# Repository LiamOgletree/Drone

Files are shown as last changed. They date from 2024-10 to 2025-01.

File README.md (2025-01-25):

Welcome! I'm designing a custom flight controller for drones. This Github page hosts all relevant files and technical details related to this effort, to include requisite project code and KiCAD schematic and PCB files.

The hardware design integrates STM32F446RE and ESP32-S3 microcontrollers, wireless and GPS (PA1616S) capabilities, and a custom IMU composed of an accelerometer and gyroscope (LSM6DSO32), barometer and temperature sensor (BMP388), and magnetometer (LIS2MDL). On the software side, I'm using STM32CubeIDE for my development environment; FreeRTOS for the OS; SPI for the LSM6DSO32, LIS2MDL, and BMP388 sensors; and DMA/UART for the PA1616S GPS receiver. Additionally, I use a Kalman Filter for state estimation &mdash; I would recommend <a href="https://github.com/rlabbe/Kalman-and-Bayesian-Filters-in-Python">this resource</a> for anyone interested in understanding Kalman Filters.

For the custom board design, I used <a href="https://www.kicad.org/">KiCAD</a> for schematic creation and the PCB layout and used <a href="https://jlcpcb.com/">JLCPCB</a> to manufacture physical boards. I'm sourcing drone components primarily from <a href="https://www.getfpv.com/">getfpv</a> (e.g., <a href="https://www.team-blacksheep.com/products/prod:sourceone_v5">this drone frame</a>) but there are many other FPV sites. Finally, for debugging purposes, I have a <a href="https://www.saleae.com/products/saleae-logic-pro-8">Saleae Logic Analyzer</a>.

See below for a functional overview of the code as it exists today:

Drone

Additionally, see below for layered 2D and rendered 3D images of the PCB design:

STM32-DRONE-FLIGHT-CONTROLLER-pcb

STM32-DRONE-FLIGHT-CONTROLLER-top

STM32-DRONE-FLIGHT-CONTROLLER-bottom

Please feel free to reach me at ogletreeliam@gmail.com with any questions or comments. Thank you!

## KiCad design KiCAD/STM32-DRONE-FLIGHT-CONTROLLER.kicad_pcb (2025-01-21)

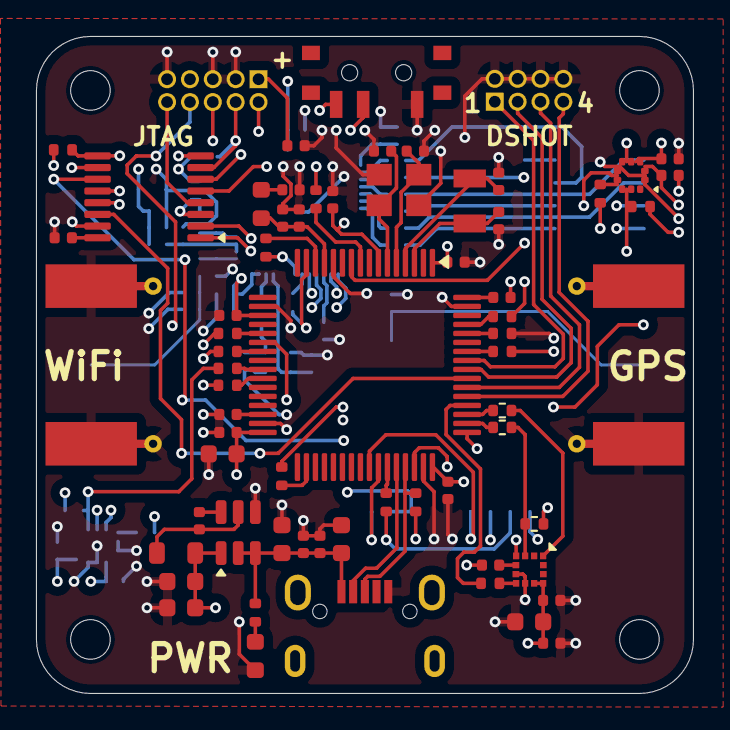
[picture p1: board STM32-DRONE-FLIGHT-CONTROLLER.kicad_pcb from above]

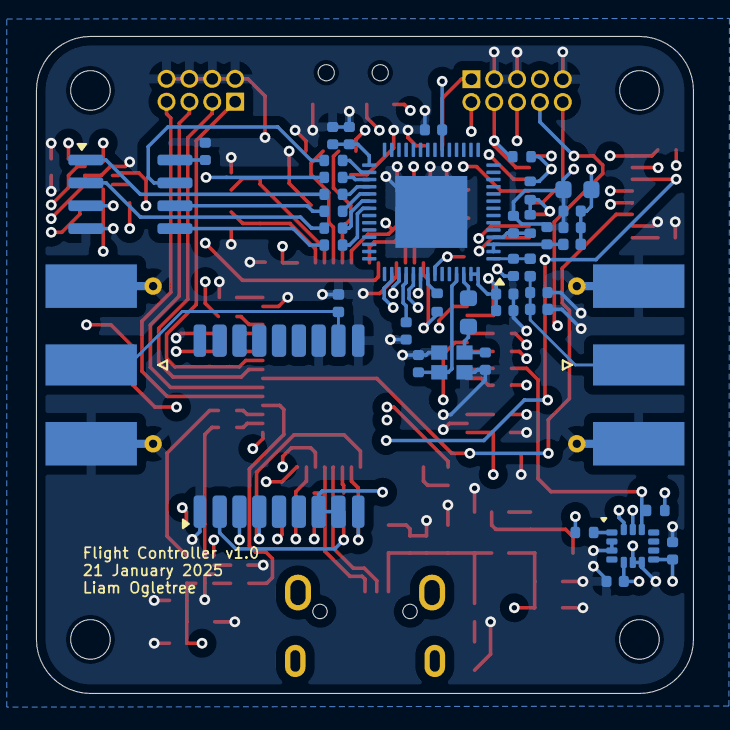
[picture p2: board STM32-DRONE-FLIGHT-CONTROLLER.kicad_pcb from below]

Board: 6 copper layers, 36.5 x 36.5 mm, 110 parts (42 on the bottom side), 88 nets.

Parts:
C1, C4, C8, C31, C44: 10uF; C_0603_1608Metric
C2, C21, C22, C23, C24, C35, C41, C45, C47, C48: 1uF; C_0402_1005Metric
C3, C5, C9, C10, C15, C16, C18, C19, C25, C26, C27, C28, C29, C30, C32, C37, C38, C39, C40, C42: 0.1uF; C_0402_1005Metric
C6, C7: 22uF; C_0603_1608Metric
C11, C12: 12.5pF; C_0402_1005Metric
C13, C14: 12pF; C_0402_1005Metric
C17: 2.2uF; C_0402_1005Metric
C20, C36: 10nF; C_0402_1005Metric
C33, C34: 10pF; C_0402_1005Metric
C43, C46: 1.2pF; C_0402_1005Metric
D1: Green; LED_0603_1608Metric
D2, D3: PESD0402-140; D_0402_1005Metric
FB1: 120R; L_0603_1608Metric
H1, H2, H3, H4: MountingHole; MountingHole_2.2mm_M2
J1: USB_B_Micro; USB_Micro-B_Wuerth_629105150521
J2: Conn_ARM_JTAG_SWD_10; PinHeader_2x05_P1.27mm_Vertical
J3: Conn_02x04_Odd_Even; PinHeader_2x04_P1.27mm_Vertical
J4, J5: Conn_Coaxial; SMA_Molex_73251-1153_EdgeMount_Horizontal
L1: 4.7uH; L_0805_2012Metric
L2: 24nH; L_0603_1608Metric
L3: 2nH; L_0402_1005Metric
L4: 2.4nH; L_0402_1005Metric
R1: 1k; R_0402_1005Metric
R2, R3, R4, R6, R7, R8, R9, R10, R18, R19, R20, R24, R25, R26, R27, R28, R29: 47R; R_0402_1005Metric
R5, R21, R22, R23, R31, R32: 10k; R_0402_1005Metric
R11, R12, R13, R14, R30: 33R; R_0402_1005Metric
R15: 1k5; R_0402_1005Metric
R16, R17: 100k; R_0402_1005Metric
SW1: SW_SPDT; SW_SPDT_PCM12
U1: AP63203WU; TSOT-23-6
U2: STM32F446RET6; LQFP-64_10x10mm_P0.5mm
U3: TMUX1574; TSSOP-16_4.4x5mm_P0.65mm
U4: ST_HLGA-10_2x2mm_P0.5mm_LayoutBorder3x2y
U5: LGA-12_2x2mm_P0.5mm
U6: LGA-14_3x2.5mm_P0.5mm_LayoutBorder3x4y
U7: MAX-M10S; ublox_MAX
U8: ESP32-S3; QFN-56-1EP_7x7mm_P0.4mm_EP4x4mm
U9: W25Q16JVSS; SOIC-8_3.9x4.9mm_P1.27mm
Y1: 32.768kHz; Crystal_SMD_3215-2Pin_3.2x1.5mm
Y2: 8MHz; Crystal_SMD_3225-4Pin_3.2x2.5mm
Y3: Crystal_GND24; Crystal_SMD_2016-4Pin_2.0x1.6mm

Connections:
+3.3V: C6.1, C7.1, C8.1, C9.1, C10.1, C15.1, C16.1, C19.1, C22.1, C23.1, C24.1, C26.2, C27.2, C28.2, C29.2, C30.2, C31.2, C32.2, C35.1, C36.1, C38.2, C39.2, C40.1, C41.1, C42.1, C44.1, C45.1, C48.1, FB1.1, J2.1 (VTref), L1.2, L3.2, R15.1, R16.1, R17.1, R21.1, R22.1, R23.1, R32.1, SW1.3 (C), U1.1 (FB), U2.1 (VBAT), U2.19 (VDD), U2.32 (VDD), U2.48 (VDD), U2.64 (VDD), U3.16 (VDD), U4.1 (VDDIO), U4.10 (VDD), U5.9 (VDD), U5.10 (VDDIO), U6.5 (VDDIO), U6.8 (VDD), U7.7 (VCC_IO), U7.8 (VCC), U8.20 (VDD3P3_RTC), U8.29 (VDD_SPI), U8.46 (VDD3P3_CPU), U8.55 (VDDA), U8.56 (VDDA), U9.8 (VCC)
+3.3VA: C20.1, C21.1, FB1.2, U2.13 (VDDA)
/Power/VBUS: C1.1, C2.1, C3.1, C4.1, J1.1 (VBUS), R1.1, U1.2 (EN), U1.3 (IN)
/STM32F446RET6/HSE_IN: C13.1, U2.5 (PH0), Y2.1
/STM32F446RET6/HSE_OUT: C14.1, U2.6 (PH1), Y2.3
/STM32F446RET6/LSE_IN: C11.1, U2.3 (PC14), Y1.1
/STM32F446RET6/LSE_OUT: C12.1, U2.4 (PC15), Y1.2
BMP388_CS: R14.1, R21.2, U4.6 (CS)
DSHOT1: J3.1, U2.57 (PB5)
DSHOT2: J3.3, U2.56 (PB4)
DSHOT3: J3.5, U2.54 (PD2)
DSHOT4: J3.7, U2.53 (PC12)
ESP32_MTCK: U3.6 (S2B), U8.44 (MTCK)
ESP32_MTDI: J2.8 (NC/TDI), U8.47 (MTDI)
ESP32_MTDO: U3.13 (S4B), U8.45 (MTDO)
ESP32_MTMS: U3.10 (S3B), U8.48 (MTMS)
ESP32_NRST: R31.1, R32.2, U3.3 (S1B)
GND: C1.2, C2.2, C3.2, C4.2, C6.2, C7.2, C8.2, C9.2, C10.2, C11.2, C12.2, C13.2, C14.2, C15.2, C16.2, C17.2, C18.2, C19.2, C20.2, C21.2, C22.2, C23.2, C24.2, C25.2, C26.1, C27.1, C28.1, C29.1, C30.1, C31.1, C32.1, C33.2, C34.2, C35.2, C36.2, C37.2, C38.1, C39.1, C40.2, C41.2, C42.2, C43.2, C44.2, C45.2, C46.2, C47.2, C48.2, D1.1 (K), D2.2 (A), D3.2 (A), J1.5 (GND), J2.3 (GND), J2.5 (GND), J2.9 (GNDDetect), J3.2, J3.4, J3.6, J3.8, J4.2 (Ext), J5.2 (Ext), R5.2, SW1.1 (A), U1.4 (GND), U2.12 (VSSA), U2.18 (VSS), U2.31 (VSS), U2.47 (VSS), U2.63 (VSS), U3.8 (GND), U3.15 (EN), U4.3 (GND), U4.8 (GND), U4.9 (GND), U5.6 (GND), U5.8 (GND), U6.2 (SDx), U6.3 (SCx), U6.6 (GND), U6.7 (GND), U7.1 (GND), U7.10 (GND), U7.12 (GND), U8.57 (GND), U9.4 (GND), Y2.2, Y2.4, Y3.2, Y3.4
LIS2MDL_CS: R8.2, R22.2, U5.3 (CS)
LSM6DSO32_CS: R3.1, R23.2, U6.12 (CS)
M10S_PPS: U2.41 (PA8), U7.4 (TIMEPULSE)
M10S_RESET: U2.42 (PA9), U7.9 (~RESET)
unnamed: C33.1, L2.1, Y3.1
unnamed: C37.1, L3.1, U8.2 (VDD3P3), U8.3 (VDD3P3)
unnamed: D1.2 (A), R1.2
unnamed: D2.1 (K), J4.1 (In), U7.11 (RF_IN)
unnamed: C46.1, D3.1 (K), J5.1 (In), L4.2
unnamed: SW1.2 (B), U3.1 (SEL)
unnamed: C5.1, U1.6 (BST)
unnamed: C5.2, L1.1, U1.5 (SW)
unnamed: R5.1, U2.60 (BOOT0)
unnamed: R11.2, U2.14 (PA0)
unnamed: R6.1, U2.21 (PA5)
unnamed: R7.1, U2.23 (PA7)
unnamed: R12.2, U2.43 (PA10)
unnamed: R8.1, U2.50 (PA15)
unnamed: R9.1, U2.26 (PB0)
unnamed: R13.2, U2.58 (PB6)
unnamed: R14.2, U2.61 (PB8)
unnamed: R10.1, U2.34 (PB13)
unnamed: R2.2, U2.9 (PC1)
unnamed: R3.2, U2.25 (PC5)
unnamed: R4.2, U2.51 (PC10)
unnamed: C17.1, U2.30 (VCAP_1)
unnamed: R18.2, U4.5 (SDO)
unnamed: C25.1, U5.5 (C1)
unnamed: R19.2, U5.7 (SDO)
unnamed: R20.2, U6.1 (SDO)
unnamed: C47.1, R31.2, U8.4 (CHIP_PU)
unnamed: C43.1, L4.1, U8.1 (LNA_IN)
unnamed: R27.2, U8.33 (SPICLK)
unnamed: R26.2, U8.32 (SPICS0)
unnamed: R29.2, U8.35 (SPID)
unnamed: R24.2, U8.30 (SPIHD)
unnamed: R28.2, U8.34 (SPIQ)
unnamed: R25.2, U8.31 (SPIWP)
unnamed: R30.2, U8.49 (U0TXD)
unnamed: C34.1, U8.53 (XTAL_N), Y3.3
unnamed: L2.2, U8.54 (XTAL_P)
SPI1_MISO: R20.1, U2.22 (PA6)
SPI1_MOSI: R7.2, U6.14 (SDI)
SPI1_SCK: R6.2, U6.13 (SCK)
SPI2_MISO: R18.1, U2.10 (PC2)
SPI2_MOSI: R2.1, U4.4 (SDI)
SPI2_SCK: R10.2, U4.2 (SCK)
SPI3_MISO: R19.1, U2.52 (PC11)
SPI3_MOSI: R9.2, U5.4 (SDI)
SPI3_SCK: R4.1, U5.1 (SCK)
SPICLK: R27.1, U9.6 (CLK)
SPICS0: R26.1, U9.1 (~CS)
SPID: R29.1, U9.5 (DI(IO0))
SPIHD: R24.1, U9.7 (IO3)
SPIQ: R28.1, U9.2 (DO(IO1))
SPIWP: R25.1, U9.3 (IO2)
STM32_NRST: C18.1, U2.7 (NRST), U3.2 (S1A)
STM32_SWCLK: U2.49 (PA14), U3.5 (S2A)
STM32_SWDIO: U2.46 (PA13), U3.11 (S3A)
STM32_SWO: U2.55 (PB3), U3.14 (S4A)
SWD_NRST: J2.10 (~RESET), U3.4 (D1)
SWD_SWCLK: J2.4 (SWCLK/TCK), R16.2, U3.7 (D2)
SWD_SWDIO: J2.2 (SWDIO/TMS), R17.2, U3.9 (D3)
SWD_SWO: J2.6 (SWO/TDO), U3.12 (D4)
UART4_MISO: R30.1, U2.15 (PA1)
UART4_MOSI: R11.1, U8.50 (U0RXD)
USART1_MISO: R12.1, U7.2 (TXD)
USART1_MOSI: R13.1, U7.3 (RXD)
USB_D+: J1.3 (D+), R15.2, U2.45 (PA12)
USB_D-: J1.2 (D-), U2.44 (PA11)

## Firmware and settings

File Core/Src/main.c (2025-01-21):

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
/* Includes ------------------------------------------------------------------*/
#include "main.h"
#include "cmsis_os.h"

/* USER CODE BEGIN Includes */
#include "taskBMP388.h"
#include "taskLIS2MDL.h"
#include "taskLSM6DSO32.h"
#include "taskPA1616S.h"
#include "taskStateMachine.h"
#include "taskShared.h"
/* USER CODE END Includes */

SPI_HandleTypeDef hspi1;

TIM_HandleTypeDef htim5;
TIM_HandleTypeDef htim11;

UART_HandleTypeDef huart1;
UART_HandleTypeDef huart2;
DMA_HandleTypeDef hdma_usart1_rx;

/* Definitions for defaultTask */
osThreadId_t defaultTaskHandle;
const osThreadAttr_t defaultTask_attributes = {
  .name = "defaultTask",
  .stack_size = 128 * 4,
  .priority = (osPriority_t) osPriorityLow,
};
/* Definitions for RunLogger */
osThreadId_t RunLoggerHandle;
const osThreadAttr_t RunLogger_attributes = {
  .name = "RunLogger",
  .stack_size = 1000 * 4,
  .priority = (osPriority_t) osPriorityBelowNormal7,
};
/* Definitions for RunBMP388 */
osThreadId_t RunBMP388Handle;
const osThreadAttr_t RunBMP388_attributes = {
  .name = "RunBMP388",
  .stack_size = 128 * 4,
  .priority = (osPriority_t) osPriorityNormal,
};
/* Definitions for RunLIS2MDL */
osThreadId_t RunLIS2MDLHandle;
const osThreadAttr_t RunLIS2MDL_attributes = {
  .name = "RunLIS2MDL",
  .stack_size = 128 * 4,
  .priority = (osPriority_t) osPriorityNormal,
};
/* Definitions for RunLSM6DSO32 */
osThreadId_t RunLSM6DSO32Handle;
const osThreadAttr_t RunLSM6DSO32_attributes = {
  .name = "RunLSM6DSO32",
  .stack_size = 128 * 4,
  .priority = (osPriority_t) osPriorityNormal,
};
/* Definitions for RunStateMachine */
osThreadId_t RunStateMachineHandle;
const osThreadAttr_t RunStateMachine_attributes = {
  .name = "RunStateMachine",
  .stack_size = 8192 * 4,
  .priority = (osPriority_t) osPriorityNormal,
};
/* Definitions for runPA1616S */
osThreadId_t runPA1616SHandle;
const osThreadAttr_t runPA1616S_attributes = {
  .name = "runPA1616S",
  .stack_size = 6000 * 4,
  .priority = (osPriority_t) osPriorityNormal,
};
/* Definitions for loggerMutex */
osMutexId_t loggerMutexHandle;
const osMutexAttr_t loggerMutex_attributes = {
  .name = "loggerMutex"
};
/* Definitions for smMutex */
osMutexId_t smMutexHandle;
const osMutexAttr_t smMutex_attributes = {
  .name = "smMutex"
};
/* Definitions for pa1616sMutex */
osMutexId_t pa1616sMutexHandle;
const osMutexAttr_t pa1616sMutex_attributes = {
  .name = "pa1616sMutex"
};
/* Definitions for loggerSemaphore */
osSemaphoreId_t loggerSemaphoreHandle;
const osSemaphoreAttr_t loggerSemaphore_attributes = {
  .name = "loggerSemaphore"
};
/* Definitions for smSemaphore */
osSemaphoreId_t smSemaphoreHandle;
const osSemaphoreAttr_t smSemaphore_attributes = {
  .name = "smSemaphore"
};
/* Definitions for pa1616sSemaphore */
osSemaphoreId_t pa1616sSemaphoreHandle;
const osSemaphoreAttr_t pa1616sSemaphore_attributes = {
  .name = "pa1616sSemaphore"
};
/* USER CODE BEGIN PV */
RingBuffer logger_ringbuffer;
RingBuffer sm_ringbuffer;
RingBuffer pa1616s_ringbuffer;
RingBuffer_t logger_ringbuffer_buf[64];
RingBuffer_t sm_ringbuffer_buf[64];
RingBuffer_t pa1616s_ringbuffer_buf[64];

TASK_ARGS task_args = {.hspi = &hspi1,
                       .huart_logger = &huart2,
                       .huart_pa1616s = &huart1,
                       .logger_ringbuffer = &logger_ringbuffer,
                       .sm_ringbuffer = &sm_ringbuffer,
                       .pa1616s_ringbuffer = &pa1616s_ringbuffer,
                       .logger_semaphore = &loggerSemaphoreHandle,
                       .sm_semaphore = &smSemaphoreHandle,
                       .pa1616s_semaphore = &pa1616sSemaphoreHandle,
                       .logger_mutex = &loggerMutexHandle,
                       .sm_mutex = &smMutexHandle};
/* USER CODE END PV */

void SystemClock_Config(void);
static void MX_GPIO_Init(void);
static void MX_DMA_Init(void);
static void MX_USART2_UART_Init(void);
static void MX_SPI1_Init(void);
static void MX_TIM5_Init(void);
static void MX_TIM11_Init(void);
static void MX_USART1_UART_Init(void);
void StartDefaultTask(void *argument);
extern void StartLogger(void *argument);
extern void StartBMP388(void *argument);
extern void StartLIS2MDL(void *argument);
extern void StartLSM6DSO32(void *argument);
extern void StartStateMachine(void *argument);
extern void StartPA1616S(void *argument);

/**
  * @brief  The application entry point.
  * @retval int
  */
int main(void)
{

  /* MCU Configuration--------------------------------------------------------*/

  /* Reset of all peripherals, Initializes the Flash interface and the Systick. */
  HAL_Init();

  /* Configure the system clock */
  SystemClock_Config();

  /* Initialize all configured peripherals */
  MX_GPIO_Init();
  MX_DMA_Init();
  MX_USART2_UART_Init();
  MX_SPI1_Init();
  MX_TIM5_Init();
  MX_TIM11_Init();
  MX_USART1_UART_Init();
  /* USER CODE BEGIN 2 */

  RingBuffer_ctor(&logger_ringbuffer, 64, logger_ringbuffer_buf);
  RingBuffer_ctor(&sm_ringbuffer, 64, sm_ringbuffer_buf);
  RingBuffer_ctor(&pa1616s_ringbuffer, 64, pa1616s_ringbuffer_buf);
  HAL_Delay(100);

  RCC->APB1ENR |= RCC_APB1ENR_TIM2EN;
  TIM5->CR1 |= TIM_CR1_CEN;

  /* USER CODE END 2 */

  /* Init scheduler */
  osKernelInitialize();
  /* Create the mutex(es) */
  /* creation of loggerMutex */
  loggerMutexHandle = osMutexNew(&loggerMutex_attributes);

  /* creation of smMutex */
  smMutexHandle = osMutexNew(&smMutex_attributes);

  /* creation of pa1616sMutex */
  pa1616sMutexHandle = osMutexNew(&pa1616sMutex_attributes);

  /* USER CODE BEGIN RTOS_MUTEX */
  /* add mutexes, ... */
  /* USER CODE END RTOS_MUTEX */

  /* Create the semaphores(s) */
  /* creation of loggerSemaphore */
  loggerSemaphoreHandle = osSemaphoreNew(64, 0, &loggerSemaphore_attributes);

  /* creation of smSemaphore */
  smSemaphoreHandle = osSemaphoreNew(64, 0, &smSemaphore_attributes);

  /* creation of pa1616sSemaphore */
  pa1616sSemaphoreHandle = osSemaphoreNew(64, 0, &pa1616sSemaphore_attributes);

  /* USER CODE BEGIN RTOS_SEMAPHORES */
  /* add semaphores, ... */
  /* USER CODE END RTOS_SEMAPHORES */

  /* USER CODE BEGIN RTOS_TIMERS */
  /* start timers, add new ones, ... */
  /* USER CODE END RTOS_TIMERS */

  /* USER CODE BEGIN RTOS_QUEUES */
  /* add queues, ... */
  /* USER CODE END RTOS_QUEUES */

  /* Create the thread(s) */
  /* creation of defaultTask */
  defaultTaskHandle = osThreadNew(StartDefaultTask, NULL, &defaultTask_attributes);

  /* creation of RunLogger */
  RunLoggerHandle = osThreadNew(StartLogger, (void*) &task_args, &RunLogger_attributes);

  /* creation of RunBMP388 */
  RunBMP388Handle = osThreadNew(StartBMP388, (void*) &task_args, &RunBMP388_attributes);

  /* creation of RunLIS2MDL */
  RunLIS2MDLHandle = osThreadNew(StartLIS2MDL, (void*) &task_args, &RunLIS2MDL_attributes);

  /* creation of RunLSM6DSO32 */
  RunLSM6DSO32Handle = osThreadNew(StartLSM6DSO32, (void*) &task_args, &RunLSM6DSO32_attributes);

  /* creation of RunStateMachine */
  RunStateMachineHandle = osThreadNew(StartStateMachine, (void*) &task_args, &RunStateMachine_attributes);

  /* creation of runPA1616S */
  runPA1616SHandle = osThreadNew(StartPA1616S, (void*) &task_args, &runPA1616S_attributes);

  /* USER CODE BEGIN RTOS_THREADS */
  /* add threads, ... */
  /* USER CODE END RTOS_THREADS */

  /* USER CODE BEGIN RTOS_EVENTS */
  /* add events, ... */
  /* USER CODE END RTOS_EVENTS */

  /* Start scheduler */
  osKernelStart();

  /* We should never get here as control is now taken by the scheduler */

  /* Infinite loop */
  /* USER CODE BEGIN WHILE */

  while (1)
  {
    /* USER CODE END WHILE */

    /* USER CODE BEGIN 3 */
  }
  /* USER CODE END 3 */
}

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
/* USER CODE BEGIN Header_StartDefaultTask */
/**
  * @brief  Function implementing the defaultTask thread.
  * @param  argument: Not used
  * @retval None
  */
/* USER CODE END Header_StartDefaultTask */
void StartDefaultTask(void *argument)
{
  /* USER CODE BEGIN 5 */

  /* Infinite loop */
  for(;;) {
    osDelay(1);
  }
  /* USER CODE END 5 */
}

/**
  * @brief  Period elapsed callback in non blocking mode
  * @note   This function is called  when TIM6 interrupt took place, inside
  * HAL_TIM_IRQHandler(). It makes a direct call to HAL_IncTick() to increment
  * a global variable "uwTick" used as application time base.
  * @param  htim : TIM handle
  * @retval None
  */
void HAL_TIM_PeriodElapsedCallback(TIM_HandleTypeDef *htim)
{
  if (htim->Instance == TIM6) {
    HAL_IncTick();
  }
}

/**
  * @brief  This function is executed in case of error occurrence.
  * @retval None
  */
void Error_Handler(void)
{
  /* USER CODE BEGIN Error_Handler_Debug */
  /* User can add his own implementation to report the HAL error return state */
  __disable_irq();
  while (1)
  {
  }
  /* USER CODE END Error_Handler_Debug */
}

#ifdef  USE_FULL_ASSERT
/**
  * @brief  Reports the name of the source file and the source line number
  *         where the assert_param error has occurred.
  * @param  file: pointer to the source file name
  * @param  line: assert_param error line source number
  * @retval None
  */
void assert_failed(uint8_t *file, uint32_t line)
{
  /* USER CODE BEGIN 6 */
  /* User can add his own implementation to report the file name and line number,
     ex: printf("Wrong parameters value: file %s on line %d\r\n", file, line) */
  /* USER CODE END 6 */
}
#endif /* USE_FULL_ASSERT */

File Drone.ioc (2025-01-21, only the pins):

Mcu.UserName=STM32F446RETx
PA0-WKUP.Signal=UART4_TX
PA1.Signal=UART4_RX
PA10.Signal=USART1_RX
PA11.Signal=USB_OTG_FS_DM
PA12.Signal=USB_OTG_FS_DP
PA13.GPIO_Label=TMS
PA13.Signal=SYS_JTMS-SWDIO
PA14.GPIO_Label=TCK
PA14.Signal=SYS_JTCK-SWCLK
PA2.GPIO_Label=USART_TX
PA2.Signal=USART2_TX
PA3.GPIO_Label=USART_RX
PA3.Signal=USART2_RX
PA5.Signal=SPI1_SCK
PA6.Signal=SPI1_MISO
PA7.Signal=SPI1_MOSI
PA8.Signal=GPIO_Output
PB0.Signal=SPI3_MOSI
PB10.Signal=GPIO_Output
PB13.Signal=SPI2_SCK
PB3.Signal=SYS_JTDO-SWO
PB4.Signal=GPIO_Output
PB6.Signal=USART1_TX
PC1.Signal=SPI2_MOSI
PC10.Signal=SPI3_SCK
PC11.Signal=SPI3_MISO
PC13.GPIO_Label=B1 [Blue PushButton]
PC13.Signal=GPXTI13
PC14-OSC32_IN.Signal=RCC_OSC32_IN
PC15-OSC32_OUT.Signal=RCC_OSC32_OUT
PC2.Signal=SPI2_MISO
PH0-OSC_IN.Signal=RCC_OSC_IN
PH1-OSC_OUT.Signal=RCC_OSC_OUT

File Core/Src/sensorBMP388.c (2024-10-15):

/*
 * BMP388.c
 *
 *  Created on: Jun 26, 2024
 *      Author: oglet
 */

#include "sensorBMP388.h"
#include "sensorShared.h"
#include "cmsis_os.h"

// TODO:
//  1. Add more precise error codes instead of blanket BMP388_FAILURE.
//  2. Refine HAL_TIMEOUT (set to ~100 ms right now).

/******************************/
/*           MACROS           */
/******************************/

#define WRITE               (0x00)
#define READ                (0x80)
#define GPIOx               (GPIOB)
#define GPIO_PINx           (GPIO_PIN_10)
#define REG_WHO_AM_I        (0x00)
#define REG_CALIBRATION     (0x31)
#define REG_PWR_CTRL        (0x1B)
#define REG_PRESSURE        (0x04)
#define REG_TEMPERATURE     (0x07)
#define ENABLE_PRESSURE     (0x01)
#define ENABLE_TEMPERATURE  (0x02)
#define NORMAL_MODE         (0x30)

/******************************/
/*          GLOBALS           */
/******************************/

// Latest temperature reading for pressure compensation function.
volatile float global_temperature;

/******************************/
/*      HELPER FUNCTIONS      */
/******************************/

static void compute_compensations(BMP388_COMP * const bmp388_comp,
                                  uint8_t const * const DATA)
{
    // Compute hard-iron compensations according to BMP388 datasheet.
    bmp388_comp->T1 =  (float)((DATA[2] << 8) | DATA[1]) * 256.f;
    bmp388_comp->T2 =  (float)((DATA[4] << 8) | DATA[3]) / 1073741824.f;
    bmp388_comp->T3 =  (float)(DATA[5]) / 281474976710656.f;
    bmp388_comp->P1 = ((float)((DATA[7] << 8) | DATA[6]) - 16384.f) / 1048576.f;
    bmp388_comp->P2 = ((float)((DATA[9] << 8) | DATA[8]) - 16384.f) / 536870912.f;
    bmp388_comp->P3 =  (float)(DATA[10]) / 4294967296.f;
    bmp388_comp->P4 =  (float)(DATA[11]) / 137438953472.f;
    bmp388_comp->P5 =  (float)((DATA[13] << 8) | DATA[12]) * 8.f;
    bmp388_comp->P6 =  (float)((DATA[15] << 8) | DATA[14]) / 64.f;
    bmp388_comp->P7 =  (float)(DATA[16]) / 256.f;
    bmp388_comp->P8 =  (float)(DATA[17]) / 32768.f;
    bmp388_comp->P9 =  (float)((DATA[19] << 8) | DATA[18]) / 281474976710656.f;
    bmp388_comp->P10 = (float)(DATA[20]) / 281474976710656.f;
    bmp388_comp->P11 = (float)(DATA[21]) / 36893488147419103232.f;
}

static void compensate_temperature(BMP388 * const bmp388,
                                   BMP388_COMP const * const bmp388_comp,
                                   float const uncomp_temp)
{
    // Compute temperature using hard-iron compensations, as detailed
    //  in the BMP388 datasheet.
    float const partial_data1 = uncomp_temp - bmp388_comp->T1;
    bmp388->temperature = \
        (partial_data1 * bmp388_comp->T2) + \
        (partial_data1 * partial_data1) * bmp388_comp->T3;
}

static void compensate_pressure(BMP388 * const bmp388,
                                BMP388_COMP const * const bmp388_comp)
{
    // Compute pressure using hard-iron compensations and temperature,
    //  as detailed in the BMP388 datasheet.
    float const temperature = global_temperature;
    float const uncomp_pres = bmp388->pressure;
    float const partial_out1 = \
        (bmp388_comp->P5) + \
        (bmp388_comp->P6 * temperature) + \
        (bmp388_comp->P7 * temperature * temperature) + \
        (bmp388_comp->P8 * temperature * temperature * temperature);
    float const partial_out2 = uncomp_pres * \
        (bmp388_comp->P1 + \
        (bmp388_comp->P2 * temperature) + \
        (bmp388_comp->P3 * temperature * temperature) + \
        (bmp388_comp->P4 * temperature * temperature * temperature));
    float const partial_out3 = (uncomp_pres * uncomp_pres) * \
        (bmp388_comp->P9 + bmp388_comp->P10 * temperature) + \
        (uncomp_pres * uncomp_pres * uncomp_pres * bmp388_comp->P11);
    bmp388->pressure = partial_out1 + partial_out2 + partial_out3;
}

/******************************/
/*       CORE FUNCTIONS       */
/******************************/

BMP388_STATUS BMP388_Setup(BMP388_COMP * const bmp388_comp,
                           SPI_HandleTypeDef * const hspi)
{
    uint8_t const TX1[] = { READ | REG_WHO_AM_I };
    uint8_t RX[22] = {0};

    // Conduct SPI transaction to retrieve constant WHO_AM_I
    //  BMP388 register value (0x50).
    if(sensor_tx_rx(TX1, sizeof(TX1) / sizeof(TX1[0]),
                    RX,  sizeof(RX)  / sizeof(RX[0]),
                    hspi, GPIOx, GPIO_PINx)
            != SENSOR_SUCCESS) {
        return BMP388_FAILURE;
    }

    // If expected value is not received, return failure.
    if(RX[1] != 0x50) {
        return BMP388_WHOAMI_FAILURE;
    }

    // Otherwise, configure the BMP388 sensor and retrieve hard-iron
    //  offset values for compensating pressure and temperature.
    uint8_t const TX2[] = {
        WRITE | REG_PWR_CTRL,
        WRITE | ENABLE_PRESSURE | ENABLE_TEMPERATURE | NORMAL_MODE,
        READ  | REG_CALIBRATION
    };

    // Conduct SPI transaction.
    if(sensor_tx_rx(TX2, sizeof(TX2) / sizeof(TX2[0]),
                    RX,  sizeof(RX)  / sizeof(RX[0]),
                    hspi, GPIOx, GPIO_PINx)
            != SENSOR_SUCCESS) {
        return BMP388_FAILURE;
    }

    // Translate raw hard-iron offsets to compensation values,
    //  according to the BMP388 datasheet.
    compute_compensations(bmp388_comp, RX);

    return BMP388_SUCCESS;
}

BMP388_STATUS BMP388_ReadTemp(BMP388 * const bmp388,
                              BMP388_COMP const * const bmp388_comp,
                              BMP388_DATA_TYPE const data_type,
                              SPI_HandleTypeDef * const hspi)
{
    uint8_t const TX[] = { READ | REG_TEMPERATURE };
    uint8_t RX[4] = {0};

    // Conduct SPI transaction to read BMP388 temperature data
    //  output registers.
    if(sensor_tx_rx(TX, sizeof(TX) / sizeof(TX[0]),
                    RX, sizeof(RX) / sizeof(RX[0]),
                    hspi, GPIOx, GPIO_PINx)
            != SENSOR_SUCCESS) {
        return BMP388_FAILURE;
    }

    // Save time stamp to compute time steps for state machine.
    bmp388->timestamp = TIM5->CNT;

    // Compute uncompensated temperature.
    float const uncomp_temp = (float)((RX[3] << 16) | (RX[2] << 8) | RX[1]);

    // Compute compensated temperature and set the global temperature.
    compensate_temperature(bmp388, bmp388_comp, uncomp_temp);
    global_temperature = bmp388->temperature;

    // If reporting raw values instead of compensated values, set
    //  temperature to the uncompensated temperature.
    if(data_type == BMP388_RAW) {
        bmp388->temperature = uncomp_temp;
    }

    return BMP388_SUCCESS;
}
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

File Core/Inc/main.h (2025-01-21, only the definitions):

#define B1_Pin GPIO_PIN_13
#define B1_GPIO_Port GPIOC
#define USART_TX_Pin GPIO_PIN_2
#define USART_TX_GPIO_Port GPIOA
#define USART_RX_Pin GPIO_PIN_3
#define USART_RX_GPIO_Port GPIOA
#define TMS_Pin GPIO_PIN_13
#define TMS_GPIO_Port GPIOA
#define TCK_Pin GPIO_PIN_14
#define TCK_GPIO_Port GPIOA

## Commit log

2024-09-09 fix spacing
    spacing fixed
    [taskLSM6DSO32.c, taskUART.c]
2024-09-26 Refinement
    Refined existing code, i.e., added error checking, reformatted for consistency, etc.
    [Drone.ioc, main.c, taskLSM6DSO32.c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]
2024-09-30 BMP388 bug fix
    added volatile temperature variable for compensate_pressure function to use
    [taskLSM6DSO32.c, taskUART.c]
2024-10-05 refinements and race conditions fixes
    added mutexes for shared resources, updated Kalman Filter, and began work on state machine task
    [Drone.ioc, main.c, taskLSM6DSO32.c]
2024-10-26 rework LSM6DSO32 and dynamically get timestamps
    [Drone.ioc, main.c, sensorLSM6DSO32.c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]
2025-01-21 Adding KiCAD design files
    [STM32-DRONE-FLIGHT-CONTROLLER.kicad_pcb, STM32-DRONE-FLIGHT-CONTROLLER.kicad_sch]

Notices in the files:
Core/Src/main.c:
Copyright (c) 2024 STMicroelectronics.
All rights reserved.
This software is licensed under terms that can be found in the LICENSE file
